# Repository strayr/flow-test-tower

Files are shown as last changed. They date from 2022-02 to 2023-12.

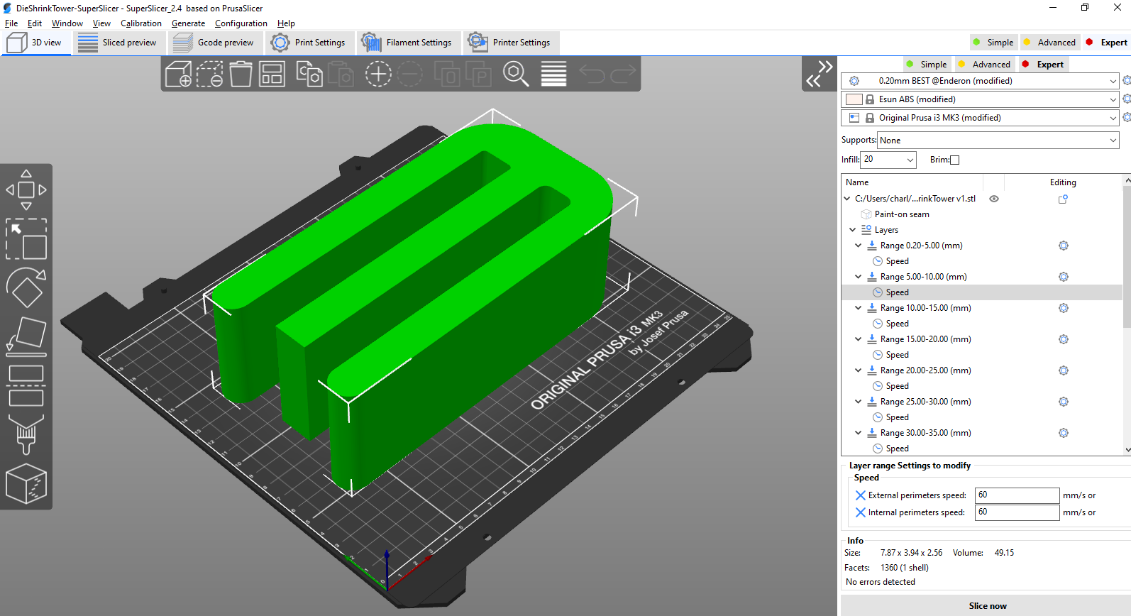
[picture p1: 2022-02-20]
images/layers.png

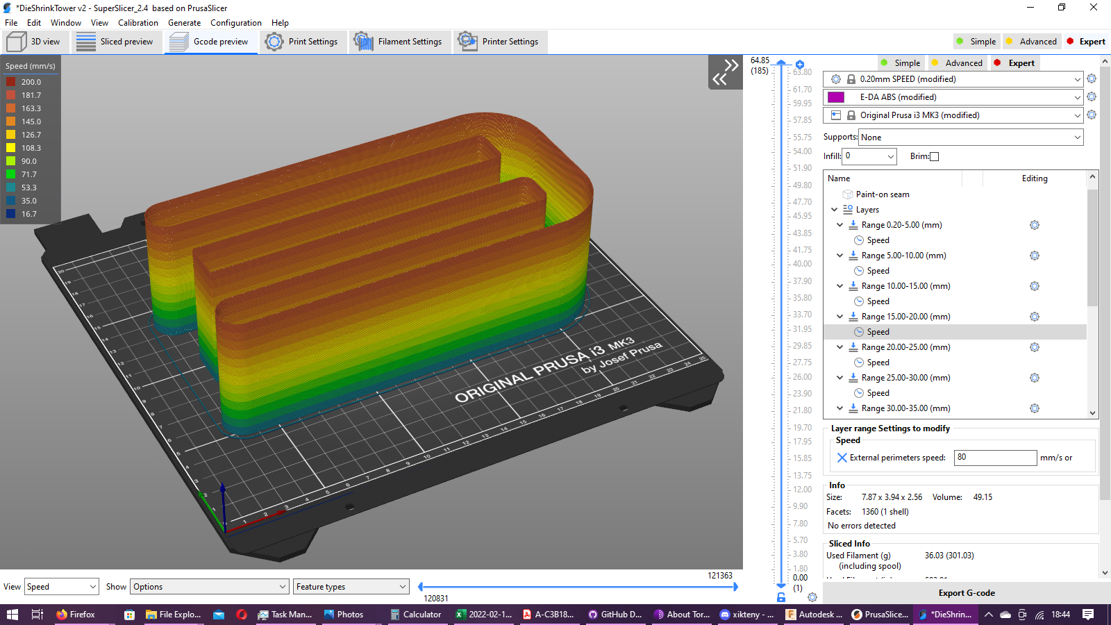
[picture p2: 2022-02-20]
images/linear_spped.png

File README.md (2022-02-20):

# Flow Test Tower
3mf and models for a printer flow test tower

## What is this?
PrusaSlicer and SuperSlicer have some really great filament profiles with volumetric flow rates set per filament for E3D V6 hotends a little conservatively but the faster print profiles ride the flow rates quite aggressively. If you have a less well supported hotend, you should be able to dial in your maximum rates. Whilst you can check for when the extruder skips doing free extrusion, die swell issues happen way before this and a geared extruder with a fairly feeble pancake stepper is capable of blowing a PTFE tube up like a balloon. By printing this tower you can find the speeds at which die swell will badly distort your print.

## How to use
Open the 3mf for your slicer, load up your printer, filament under test and the quality profile you wish to use, make changes as shown in **Slicer Settings** below. Look at the [layers set up in the window on the right](images/layers.png) and check the speeds are sensible for your hotend and motion system, adjust if not. Consider a taller layer height (0.75 * nozzle width) and a slightly wider extrusion width (upto 1.5 * nozzle width) to get higher flow at lower speeds and exaggerate die shrink effects. Remember this will increase your volumentric flow rate so record that not the peak linear speed achieved.

Check the seam is painted on to one of the sharp corners. It will look awful, but we're suck on one perimeter without vase mode. Consider not using `retract on layer change`, `wipe` or `zhop` features. 

 Hit slice now and check the [linear speed changes at each step height](images/linear_spped.png). Check the [volumetric flow visualisation](images/filament_vol_speed.png), and take a screenshot, this will be what we take our measurements from.

## Interpreting Results
Ignore the sharp corners. Thy're there to attract seams. They should be painted on one of them. With multiple vertical shells you won't have artifacts here. If the extruder starts skipping steps, stop. If the print starts curling up badly that's the dreaded die shrink, stop. Measure the height of the failure. Cross referecne it to the volumetric flow visualisation we looked at earlier. Use the last good looing step on the tower as the new volumetric flow cap for that filament. Don't forget to change the cooling settings back before you save the filament profile. 

## Slicer Settings
- Filament Settings
  Use your regular profile for the filament under test with the following changes:
  - Filament (SuperSlicer)
    - Max Volumetric Speed: 99 (or some limit just above what the tower hits)
    - Max Speed: 0 (or something higher than the tower asks for, may be greyed out)
  - Advanced (PrusaSlicer)
    - Print Speed Override: 99 (or some limit just above what the tower hits)
  - Cooling
    - layer time goal: 0
- Print Settings
  Use your regular quality and layer height/width profile
  - Layers and Perimeters
    - Vertical Shells
      - Perimeters: 1
    - Horizontal Shells
      - Bottom: 3 (suggested, just to keep the model stuck)
      - Top: 0
  - Infill
    - Fill Density: 0%
  - Skirt and Brim
    -  A brim is recommended for ABS, you know your printer. 
  - Speed
    We override most of this, so just make sure four first layer, perimeter and solid infill settings are sane
    - Auto Speed
      - Max Print Speed: Set above what you set in the tower, this is enforced
      - Max Volumetric Speed:  99 (or some limit just above what the tower hits)
  - Machine Limits
    - Make sure you can achieve the speeds the tower requests.
    - TODO
  - TODO retract on layer / wipe
  
## FAQ
- Will you support Cura?
  - No. Not until cura supports volumetric flow caps and sensible separation of printer and filament settings from the quality intent profiles.
- Can you make a faster/slower version
  - Edit the speed changes at each layer yourself. Send me a PR. I might add more as I use them.

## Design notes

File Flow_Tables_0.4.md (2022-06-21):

## 0.4 mm nozzle
 - 0.45mm extrusion width
 - slic3r flow math
 - 0.2mm layer height

| Vol Flow  | Linear speed |
|---|---|
| mm3/s |  mm/s |
| 7 | 86 |
| 8	 | 98 |
| 9	 | 111 |
| 10 | 123 |
| 11 | 135 |
| 12 | 147 |
| 13 | 160 |
| 14 | 172 |
| 15 | 184 |
| 16 | 197 |
| 17 | 209 |
| 18 | 221 |
| 19 | 233 |
| 20 | 246 |
| 21 | 258 |
| 22 | 270 |
| 23 | 282 |
| 24 | 295 |
| 25 | 307 |

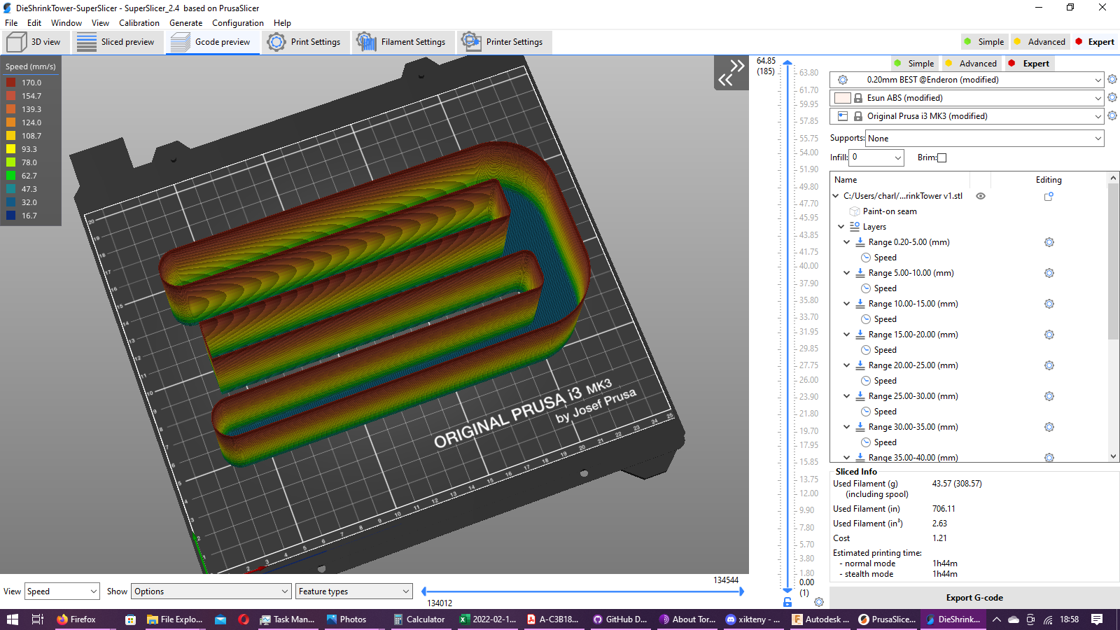
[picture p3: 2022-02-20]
images/solid_infill.png

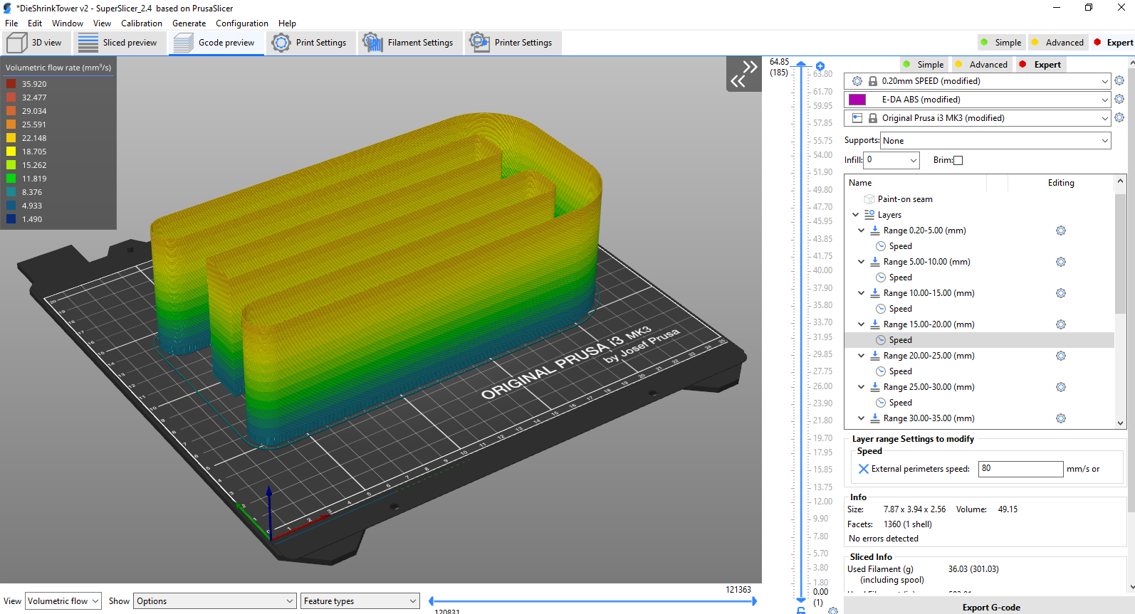
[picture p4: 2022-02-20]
images/vol_flow.png

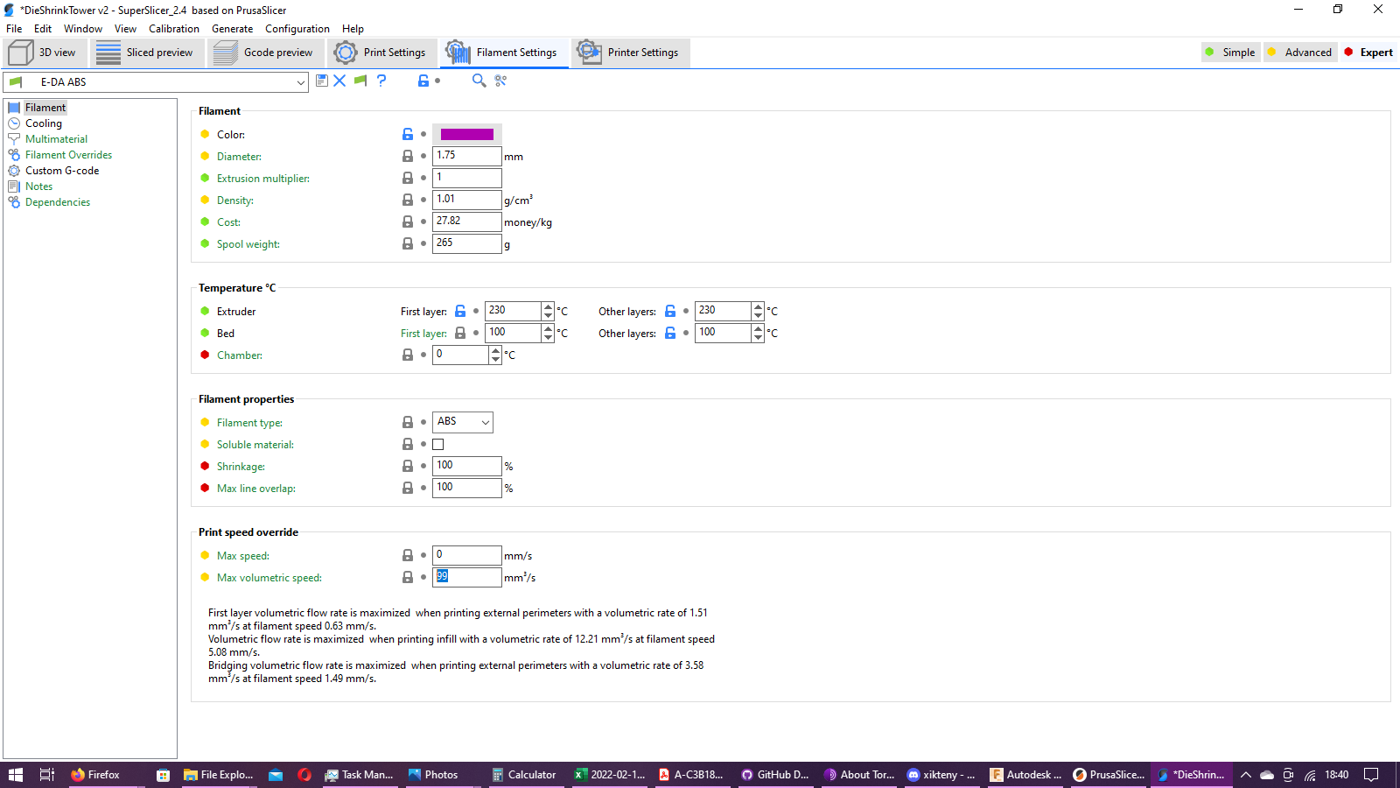
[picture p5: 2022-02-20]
images/filament_vol_speed.png

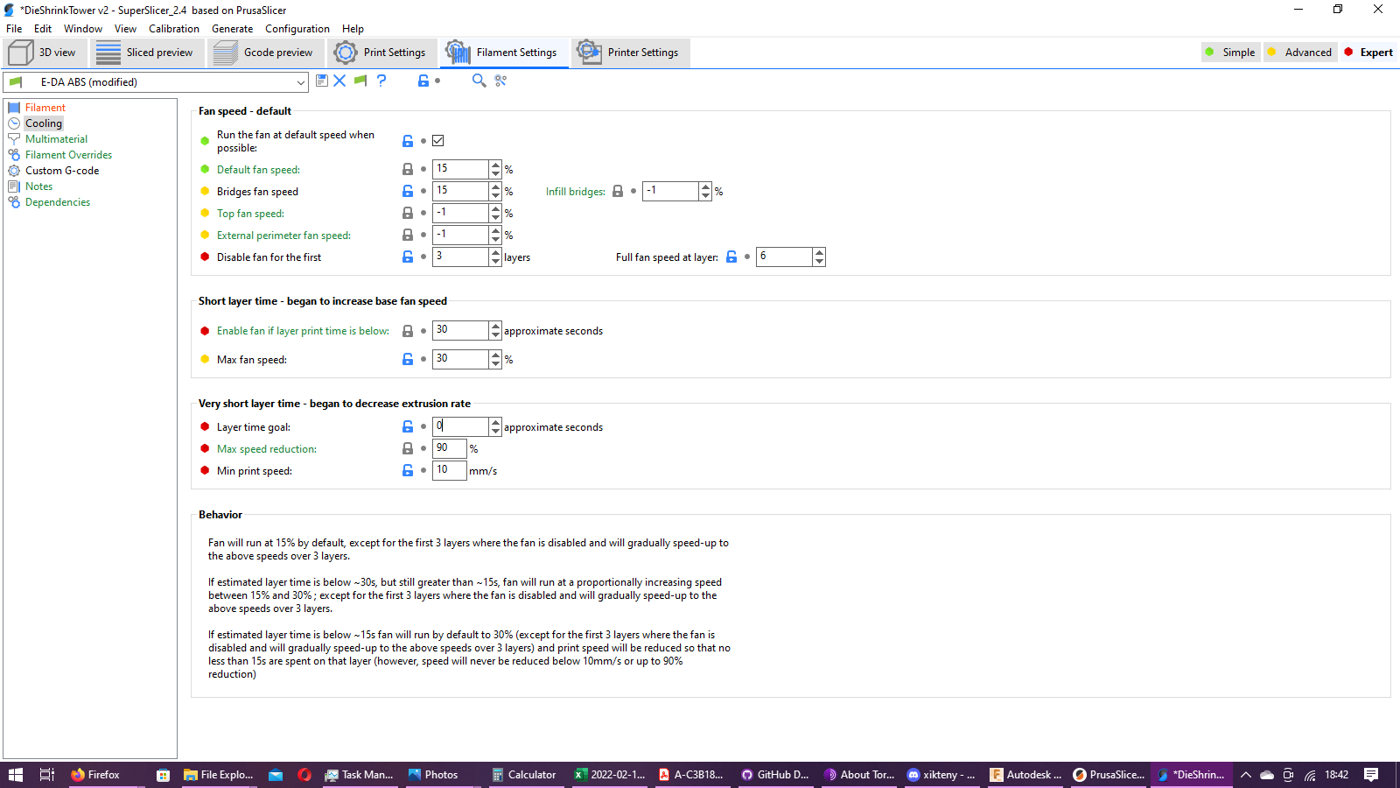
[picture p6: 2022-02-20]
images/layer_time.png

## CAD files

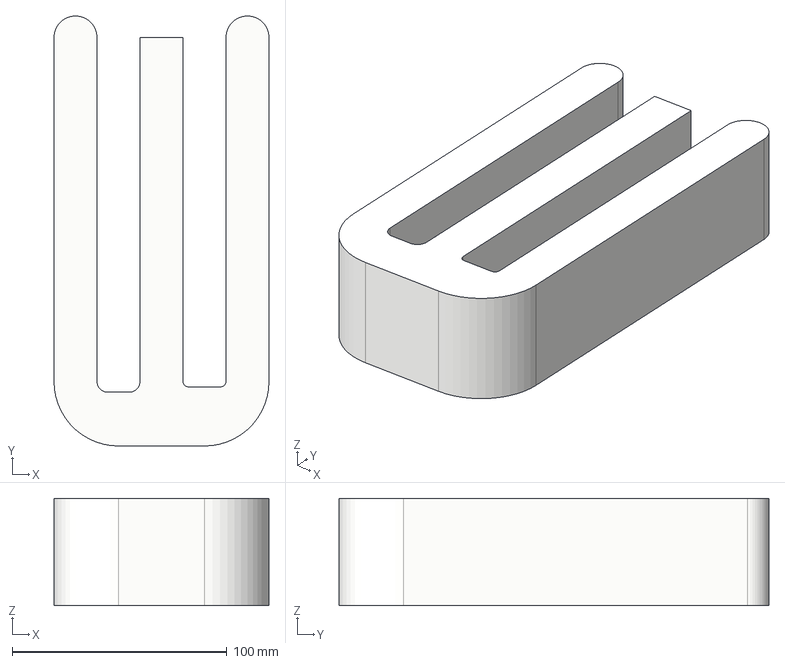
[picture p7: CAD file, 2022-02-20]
CAD/DieShrinkTower v1.step
100.0 x 200.0 x 50.0 mm

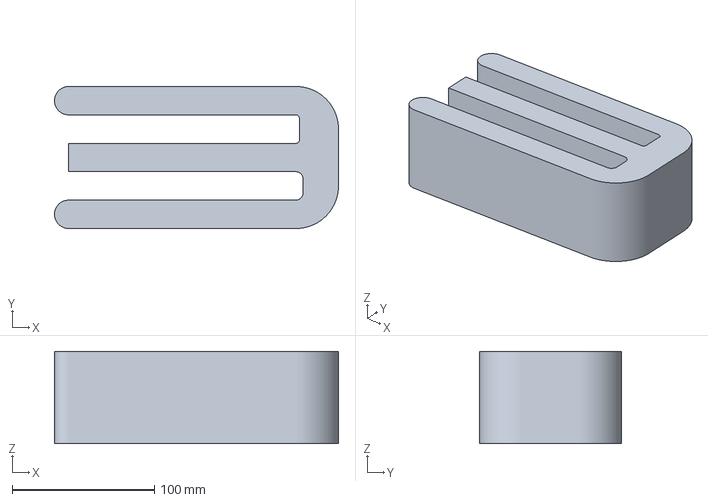
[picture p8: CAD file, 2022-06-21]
DieShrinkTower-0.4-LowFlow-SuperSlicer.3mf
200.0 x 100.0 x 65.0 mm

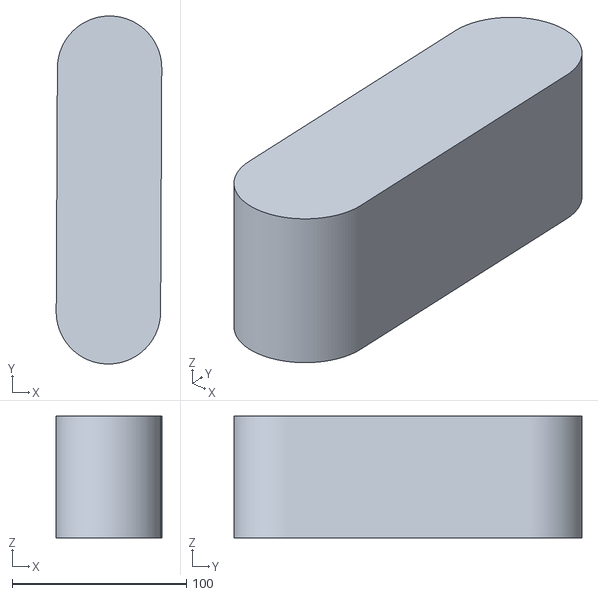
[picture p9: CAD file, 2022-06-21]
simple_tower.stl
60.7 x 200.0 x 70.0

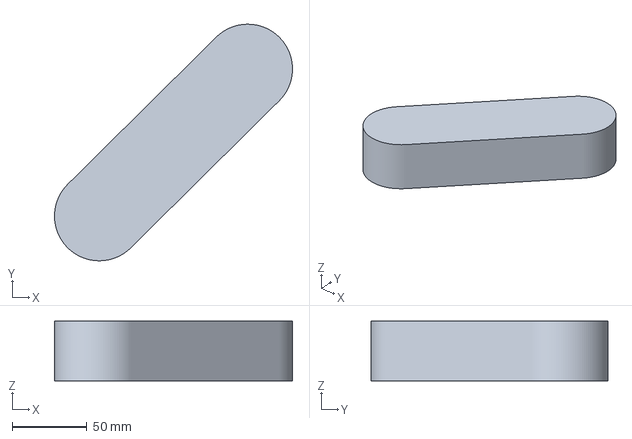
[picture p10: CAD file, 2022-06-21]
DieShrinkTower-0.4-Fast.3mf
159.5 x 158.5 x 40.0 mm

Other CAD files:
DieShrinkTower-0.4-LowFlow-TwinWall-SuperSlicer.3mf
DieShrinkTower-0.6-HighFlow-SuperSlicer.3mf
DieShrinkTower-0.6-HighFlow-PrusaSlicer.3mf
CAD/DieShrinkTower v1.f3d

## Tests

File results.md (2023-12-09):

## Results
The following are for guidance only
- Ankun PET-G at 235C
  - 0.6MM CHT: gaps appear in print at 22mm3/s, looks great up until that point
  - 0.4mm reprap/v6 gaps appear at 13mm3/s, starts looking stripey at around 11mm3/s
- Anycubic PLA at 210C
  - 0.6mm CHT: failures at 28mm3/s
  - 0.4mm reprap/v6: failures at 15mm3/s, prints well at 14mm3/s
  - 0.4mm E3D Revo Voron: failures at 15mm3/s, prints well at 14mm3/s
- eSun ABS+ at 255C
  - 0.6mm CHT: Completed 34mm3/s tower with no failures, currently doing much printing at 30mm/s without issue
  - 0.4mm reprap/v6: skipped extrusions at 18mm3/s, suspect it's good for 15mm3/s printing
- 3dQF ABS at 300C
  - 0.4mm rippling to walls at 22mm3/s, failure at 24mm3/s. Perfect up to and including 20mm3/s

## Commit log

2022-02-20 initial upload
    [DieShrinkTower v1.f3d, DieShrinkTower v1.step, DieShrinkTower-PrusaSlicer.3mf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]
2022-03-02 mark 0.6 versions as 0.6
    [DieShrinkTower-0.4-LowFlow-SuperSlicer.3mf, DieShrinkTower-0.6-HighFlow-PrusaSlicer.3mf, DieShrinkTower-0.6-HighFlow-SuperSlicer.3mf]
2022-06-21 further use with a smaller tower
    [DieShrinkTower-0.4-Fast.3mf, DieShrinkTower-0.4-LowFlow-SuperSlicer.3mf, DieShrinkTower-0.4-LowFlow-TwinWall-SuperSlicer.3mf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]
